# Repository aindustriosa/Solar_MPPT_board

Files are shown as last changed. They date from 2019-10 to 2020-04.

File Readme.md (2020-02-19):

# Propósito
Con este proxecto pretendemos crear unha pequena plataforma educacional de xestión de enerxía solar baseada no Hardware e Software empregado por un dos equipos da Industriosa participante nas edicións 2018 e 2019 da Regata Solar de Marine Instruments coa que obtivemos a victoria en ambas edicións na categoría Open.

https://www.regatasolar.org/

A idea é que o sistema sexa o suficientemente sinxelo de montar e integrar que poida ser usado polos equipos de estudantes.

# Técnica

A complexidade de construir un vehículo solar sen acumulación de enerxía radica en conseguir exprimir ó máximo as posibilidades do panel solar.
Os paneles entregan enerxía eléctrica seguindo unha curva característica que fai necesaria unha xestión intelixente da demanda do sistema de propulsión. É necesario atopar o punto de máxima potencia: se demandamos menos do que o panel é capaz de entregar, desaproveitamos enerxía, e se demandamos máis do que é capaz de entregar, o panel vense abaixo e a potencia entregada cae dramáticamente ata provocar un apagado do sistema.

A continuación unha curva característica de entrega de potencia dun panel solar:

<p align="center">
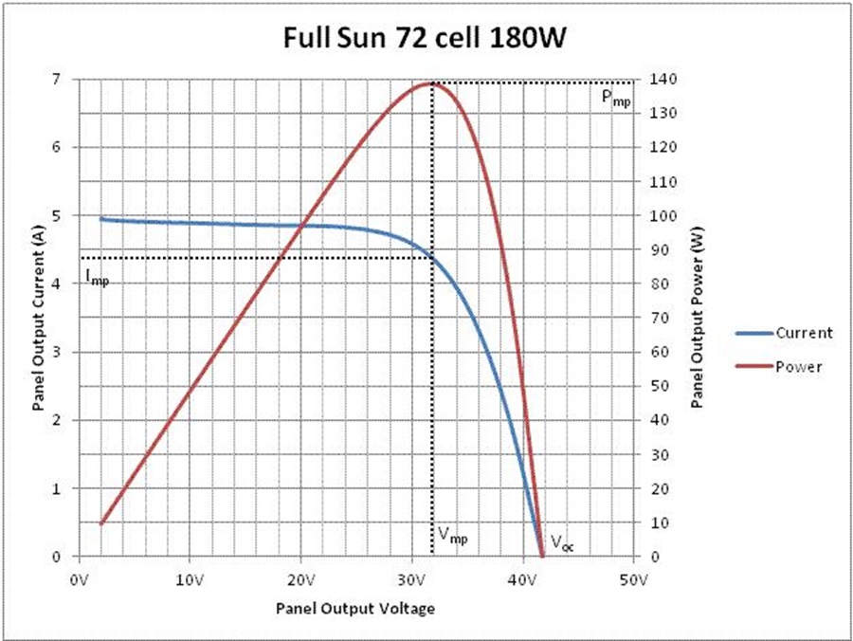
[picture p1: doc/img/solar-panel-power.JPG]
  
</p>

A estratexia seguida para conseguir o propósito consiste en monitorizar constantemente a corrente e tensión entregadas polo panel (e, por tanto, a potencia) e modular mediante un algoritmo software a demanda do motor de propulsión para conseguir en todo momento a máxima potencia disponible.
Este algoritmo ten que ser capaz de auto-adaptarse para facer fronte ás cambiantes condicións nas que o panel se atopa:
* Cambios na radiación solar
* Modificación na posición do panel con respecto do sol
* Cambios na resistencia do motor segundo as condicións dinámicas da embarcación
* ...

# Hardware

A PCB conta con tódolos seus componentes en montaxe Through Hole (Furado pasante) e módulos insertables:
* Arduino Nano
* INA219
* Bluetooth HC-05

<p align="center">
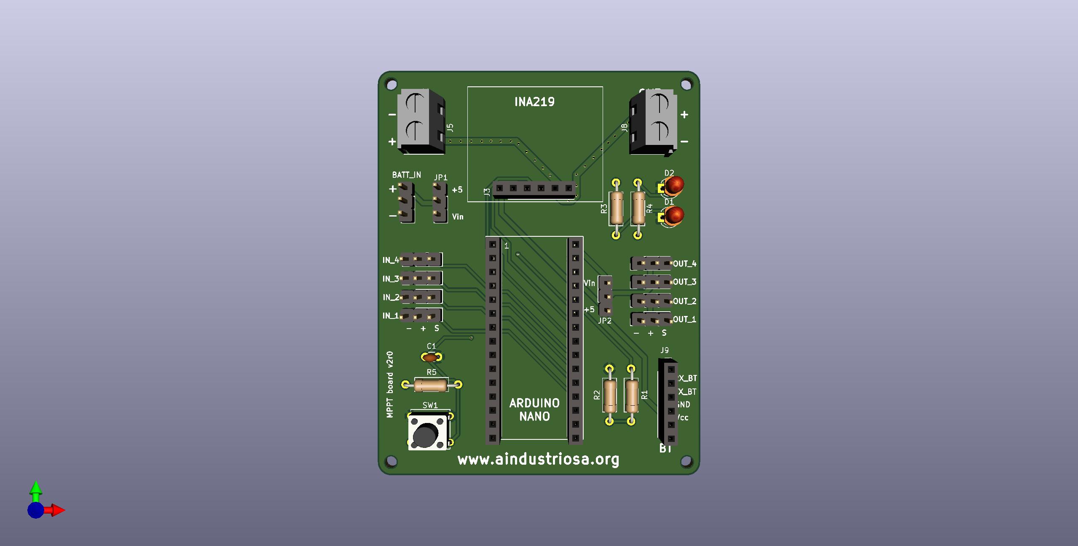
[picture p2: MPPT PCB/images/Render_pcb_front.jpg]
  
</p>

E conexións cos diferentes elementos que compoñen toda a electróncia do barco solar:
* Entrada de panel solar
* Saída de alimentación para o ESC
* Entrada de batería (receptor R/C)
* 4x Entradas PWM de sináis provintes do receptor de R/C
* 4x Saídas PWM para ESC, Servos, ...
* Conexión módulo Bluetooth HC05

Esquema básico de montaxe:

<p align="center">
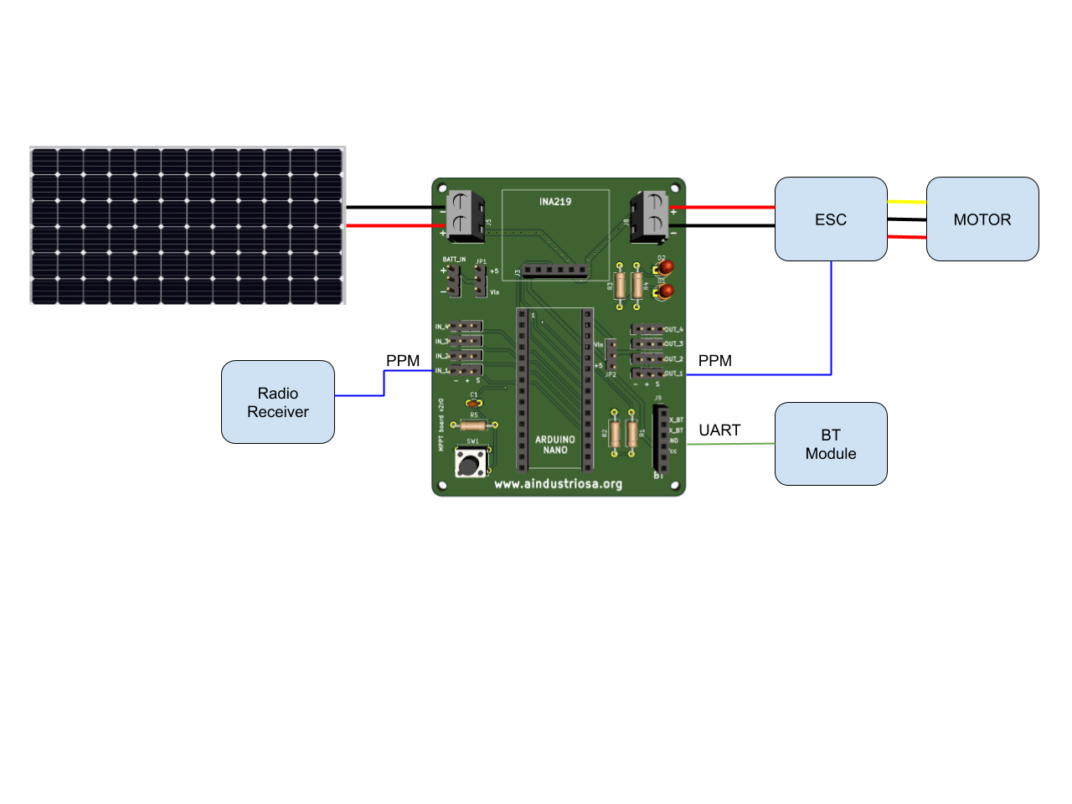
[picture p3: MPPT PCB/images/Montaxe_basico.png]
  
</p>

Os jumpers JP1 e JP2 sirven para conectar os rails de 5V e/ou Vin cos pines de alimentación das entradas e saídas PPM.
Nesta montaxe, se queremos alimentar todo o sistema a través do BEC do ESC conectaremos JP2 con Vin (caso de BEC de 6V) ou con +5V (caso de BEC de 5V). Para alimentar o receptor de radio, conectaremos JP1 para que no pin de alimentación das entradas esté disponible +5V ou Vin, según se desexe.

Na wiki do proxecto detállase o pinout dos diferentes conectores. Recoméndase revisar o esquemático para ter completamente claro o uso de estos jumpers.

https://github.com/aindustriosa/Solar_MPPT_board/wiki

### NOTA: A PCB do INA219 debe ser modificada para poder medir corrente no rango que entrega o panel. Recoméndase sustituir a resisntencia de Shunt orixinal de 0R1 por unha de 0R025.

# Software

A peza principal do código é unha implementación do algoritmo MPPT "Perturb and Observe".
Sirva como guía para comprender a implementación o seguinte documento:

http://ww1.microchip.com/downloads/en/appnotes/00001521a.pdf

En esencia, o algoritmo adapta a demanda que se fai do motor do seguinte modo:
1. Mide Corrente entregada polo panel
2. Mide a Tensión á saída do panel
3. Calcula a potencia
4. Compara coa potencia na anterior iteración
5. Incrementa ou decrementa PWM (ver grafo)

<p align="center">
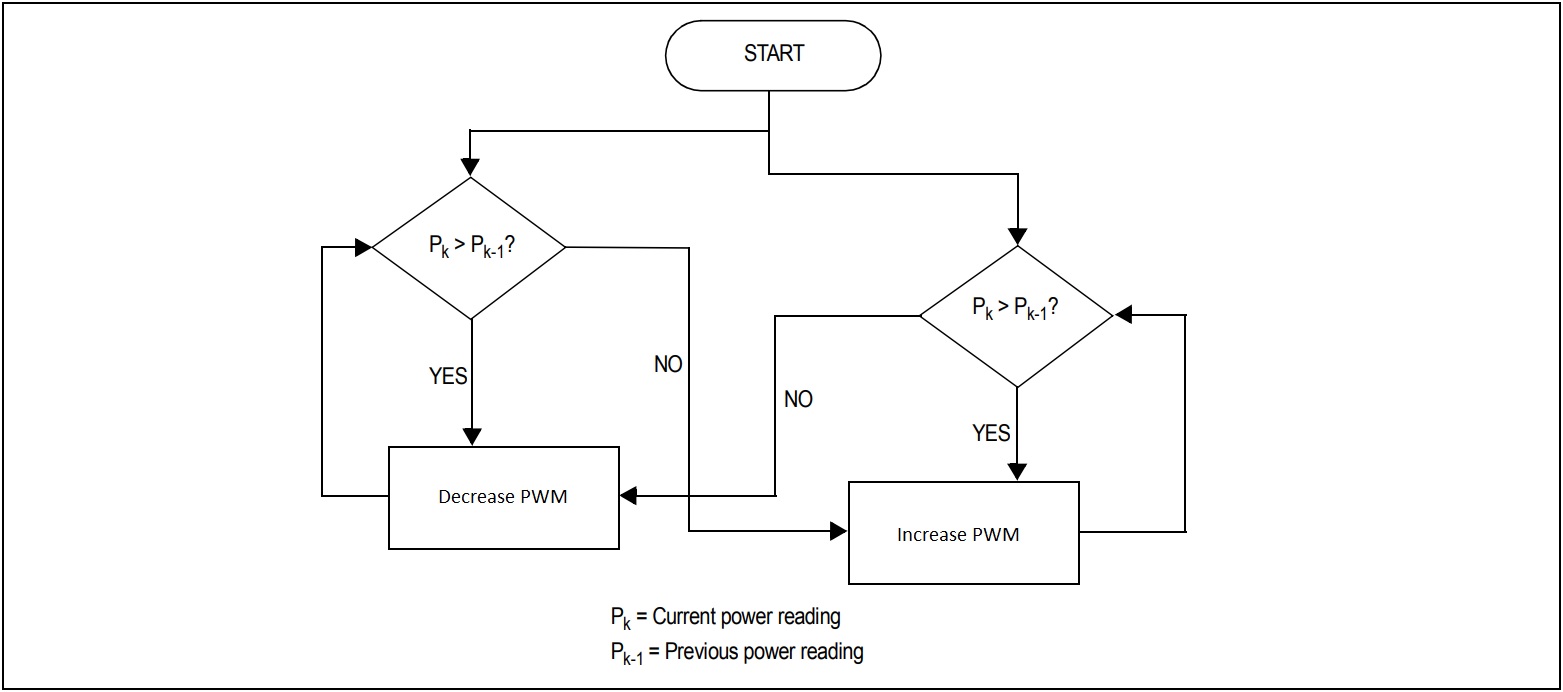
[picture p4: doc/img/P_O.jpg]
  
</p>

# Licenza

## Hardware

Diseñado por Luis Miranda e Hernán Serrano baixo licenza CERN OPEN HARDWARE LICENCE v1.2 http://www.ohwr.org/
Esta licenza aplica ós deseños Hardware e documentación contida na carpeta 'MPPT PCB' de este repositorio.

Designed by Luis Miranda & Hernán Serrano under CERN OPEN HARDWARE LICENCE v1.2 http://www.ohwr.org/
This license applies to hardware designs and documentation which reside in the 'MPPT PCB' folder of this repository.

## Software

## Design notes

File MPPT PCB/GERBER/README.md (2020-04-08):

Estos Gerbers foron enviados a JLCPCB.com

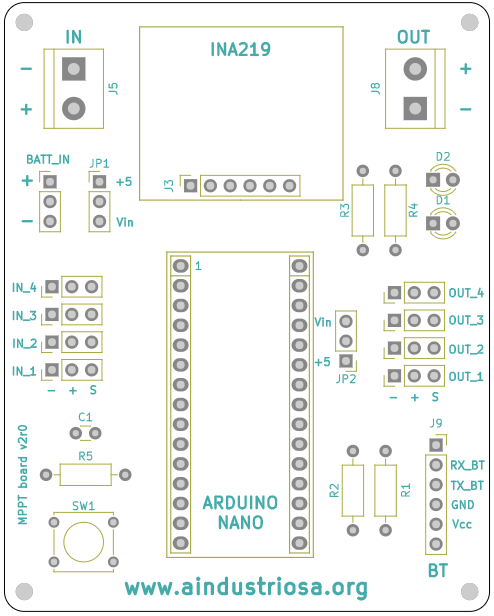
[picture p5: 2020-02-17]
MPPT PCB/images/board_pinout.png

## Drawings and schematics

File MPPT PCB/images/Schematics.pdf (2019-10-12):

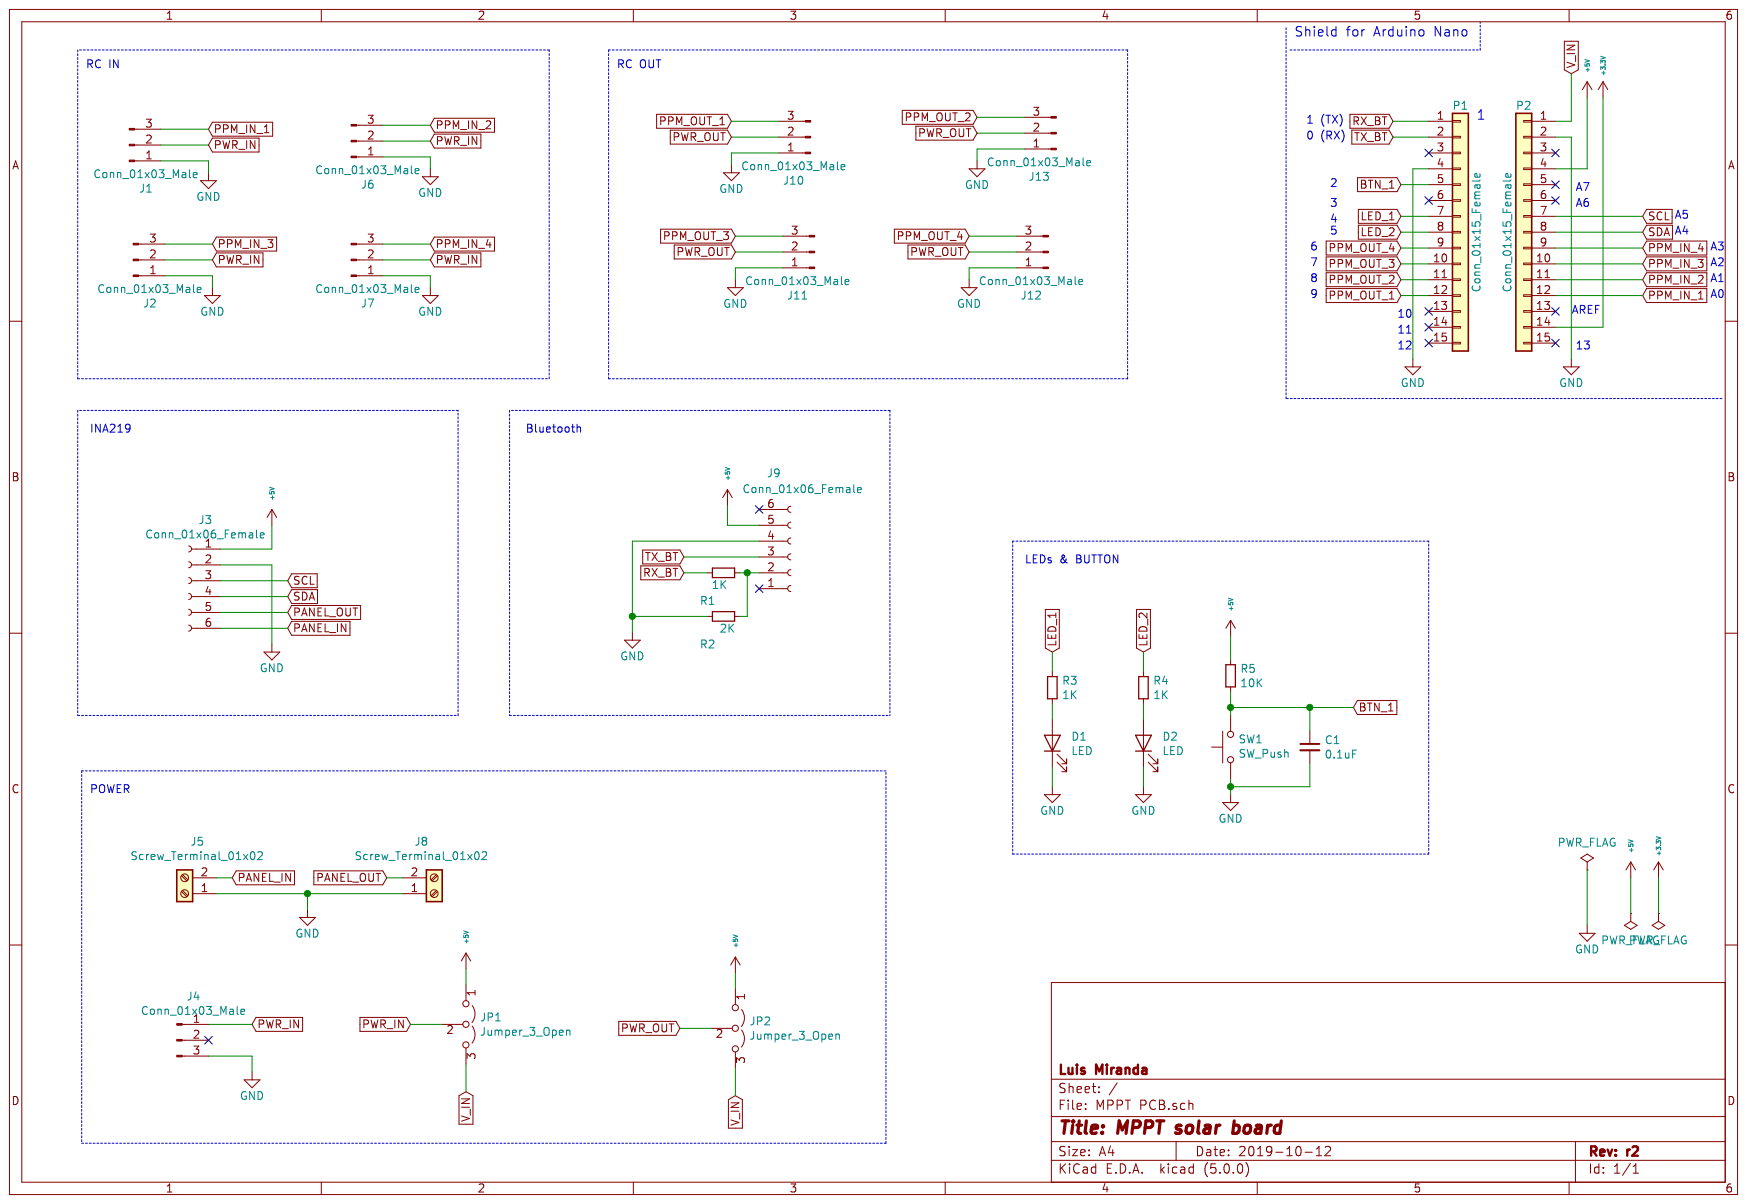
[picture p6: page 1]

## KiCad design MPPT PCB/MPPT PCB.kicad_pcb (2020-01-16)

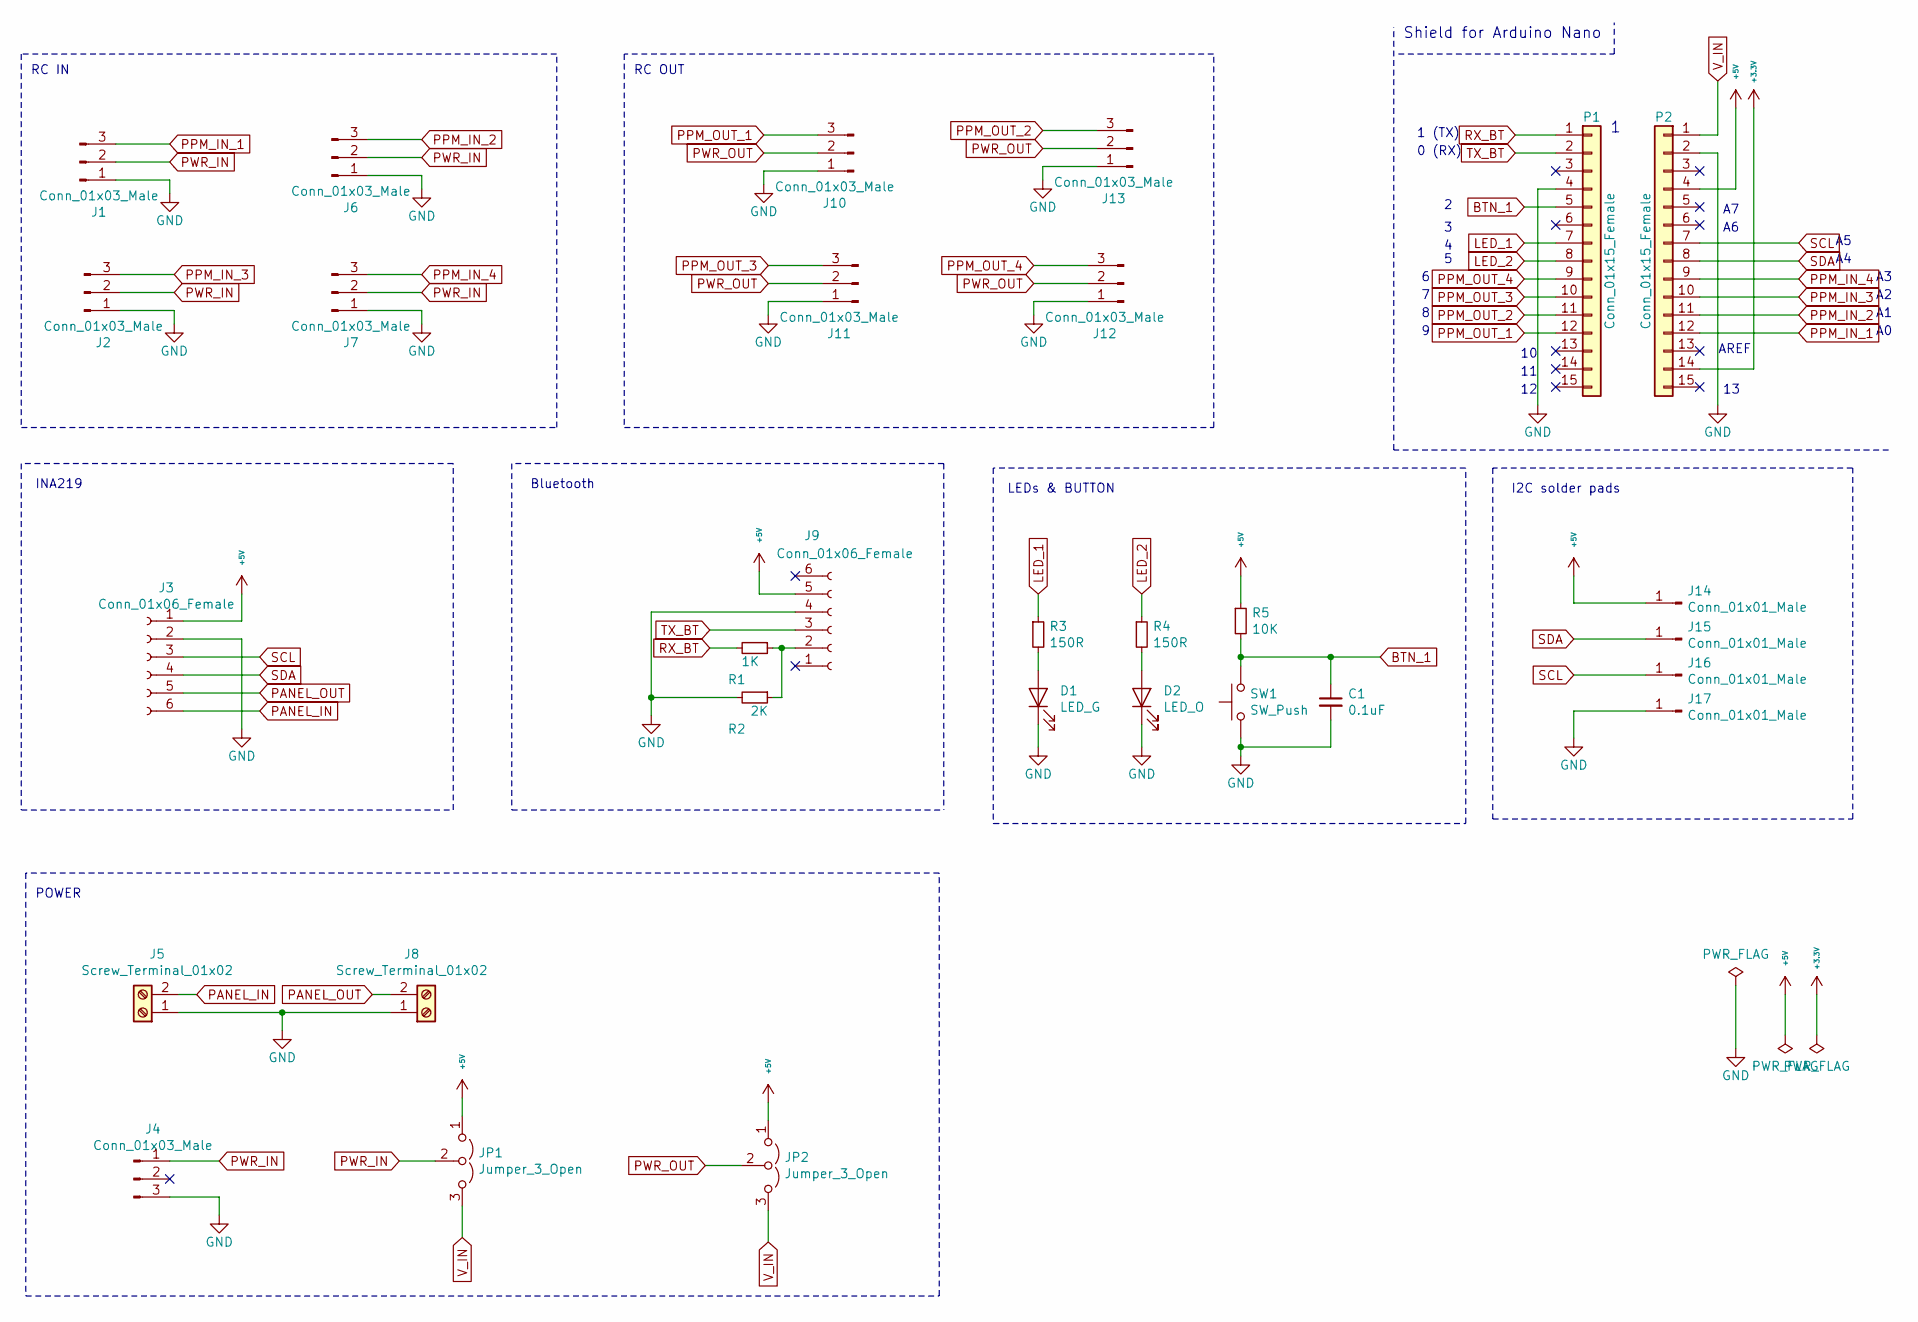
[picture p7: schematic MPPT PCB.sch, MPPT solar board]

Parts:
C1: 0.1uF; C_Disc_D3.0mm_W1.6mm_P2.50mm; DIGIKEY_PN 478-3192-ND
D1: LED_G; LED_D3.0mm; DIGIKEY_PN 732-5008-ND
D2: LED_O; LED_D3.0mm; DIGIKEY_PN 732-5010-ND
J1, J2, J4, J6, J7, J10, J11, J12, J13: Conn_01x03_Male; PinHeader_1x03_P2.54mm_Vertical; DIGIKEY_PN 732-5316-ND
J3, J9: Conn_01x06_Female; PinSocket_1x06_P2.54mm_Vertical; DIGIKEY_PN SAM1213-06-ND
J5, J8: Screw_Terminal_01x02; TerminalBlock_bornier-2_P5.08mm; DIGIKEY_PN A98076-ND
J14, J15, J16, J17: Conn_01x01_Male; Test_Point_2.67x1.02mm
JP1, JP2: Jumper_3_Open; PinHeader_1x03_P2.54mm_Vertical; DIGIKEY_PN 732-5316-ND
P1, P2: Conn_01x15_Female; Socket_Strip_Arduino_1x15; DIGIKEY_PN SAM1213-15-ND
R1: 1K; R_Axial_DIN0207_L6.3mm_D2.5mm_P10.16mm_Horizontal; DIGIKEY_PN CF14JT1K00CT-ND
R2: 2K; R_Axial_DIN0207_L6.3mm_D2.5mm_P10.16mm_Horizontal; DIGIKEY_PN CF14JT2K00CT-ND
R3, R4: 150R; R_Axial_DIN0207_L6.3mm_D2.5mm_P10.16mm_Horizontal; DIGIKEY_PN CF14JT150RCT-ND
R5: 10K; R_Axial_DIN0207_L6.3mm_D2.5mm_P10.16mm_Horizontal; DIGIKEY_PN CF14JT10K0CT-ND
SW1: SW_Push; SW_Tactile_Straight_KSA0Axx1LFTR; DIGIKEY_PN CKN12261-ND

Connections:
+3V3: P2.14
+5V: J3.1, J9.5, J14.1, JP1.1 (A), JP2.1 (A), P2.4, R5.1
BTN_1: C1.1, P1.5, R5.2, SW1.2
GND: C1.2, D1.1 (K), D2.1 (K), J1.1, J2.1, J3.2, J4.3, J5.1, J6.1, J7.1, J8.1, J9.4, J10.1, J11.1, J12.1, J13.1, J17.1, P1.4, P2.2, R2.2, SW1.1
LED_1: P1.7, R3.1
LED_2: P1.8, R4.1
unnamed: D1.2 (A), R3.2
unnamed: D2.2 (A), R4.2
unnamed: J9.2, R1.1, R2.1
PANEL_IN: J3.6, J5.2
PANEL_OUT: J3.5, J8.2
PPM_IN_1: J1.3, P2.12
PPM_IN_2: J6.3, P2.11
PPM_IN_3: J2.3, P2.10
PPM_IN_4: J7.3, P2.9
PPM_OUT_1: J10.3, P1.12
PPM_OUT_2: J13.3, P1.11
PPM_OUT_3: J11.3, P1.10
PPM_OUT_4: J12.3, P1.9
PWR_IN: J1.2, J2.2, J4.1, J6.2, J7.2, JP1.2 (C)
PWR_OUT: J10.2, J11.2, J12.2, J13.2, JP2.2 (C)
RX_BT: P1.1, R1.2
SCL: J3.3, J16.1, P2.7
SDA: J3.4, J15.1, P2.8
TX_BT: J9.3, P1.2
V_IN: JP1.3 (B), JP2.3 (B), P2.1

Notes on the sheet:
Shield for Arduino Nano
1 (TX)
0 (RX)
AREF
RC IN
RC OUT
INA219
Bluetooth
POWER
LEDs & BUTTON
I2C solder pads

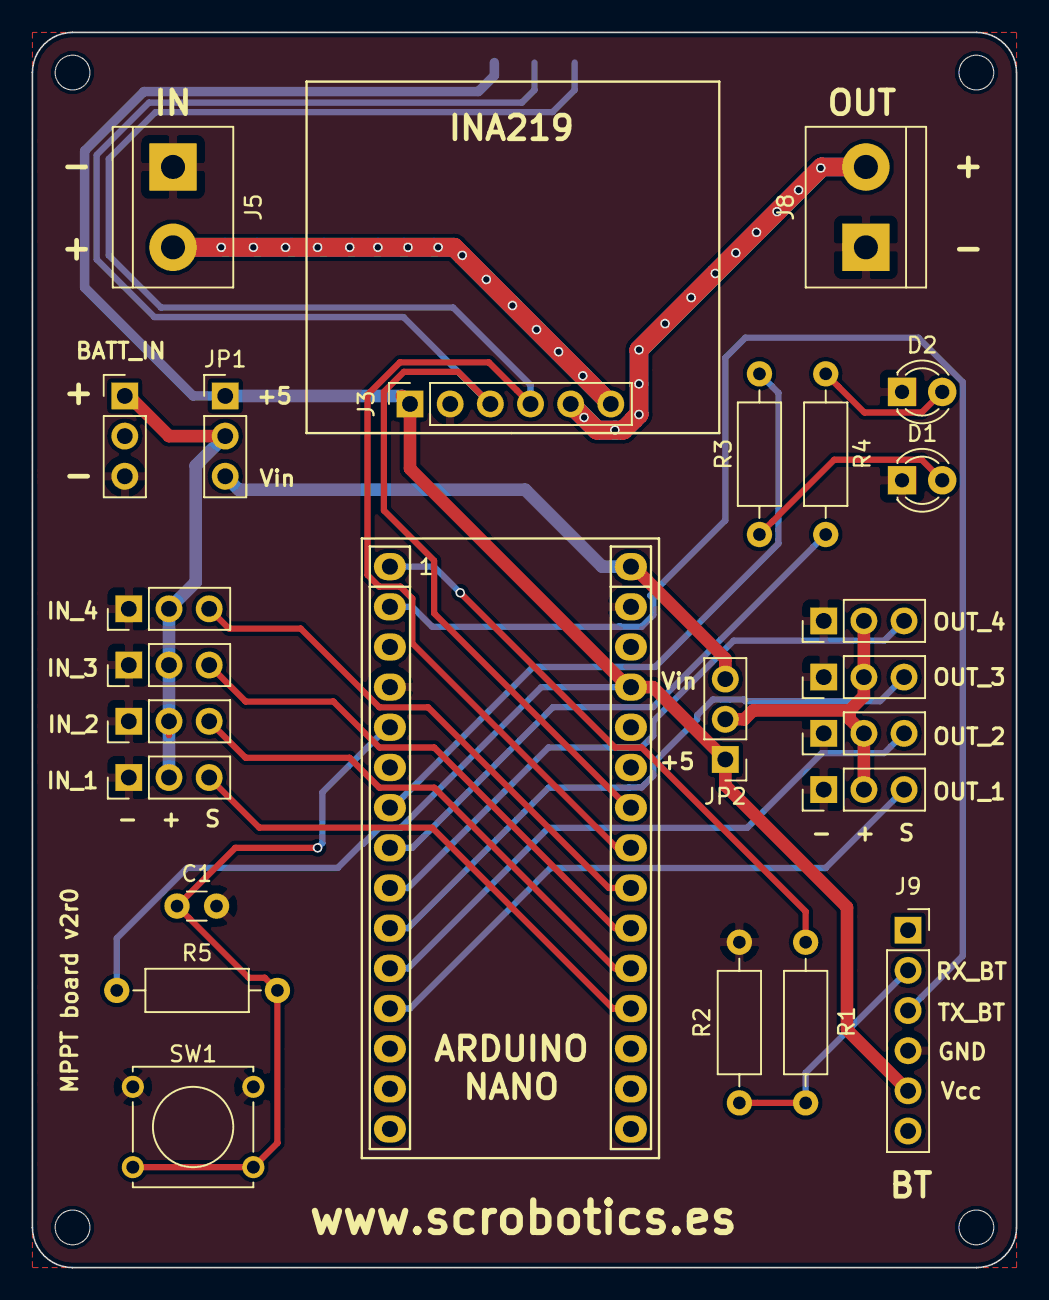
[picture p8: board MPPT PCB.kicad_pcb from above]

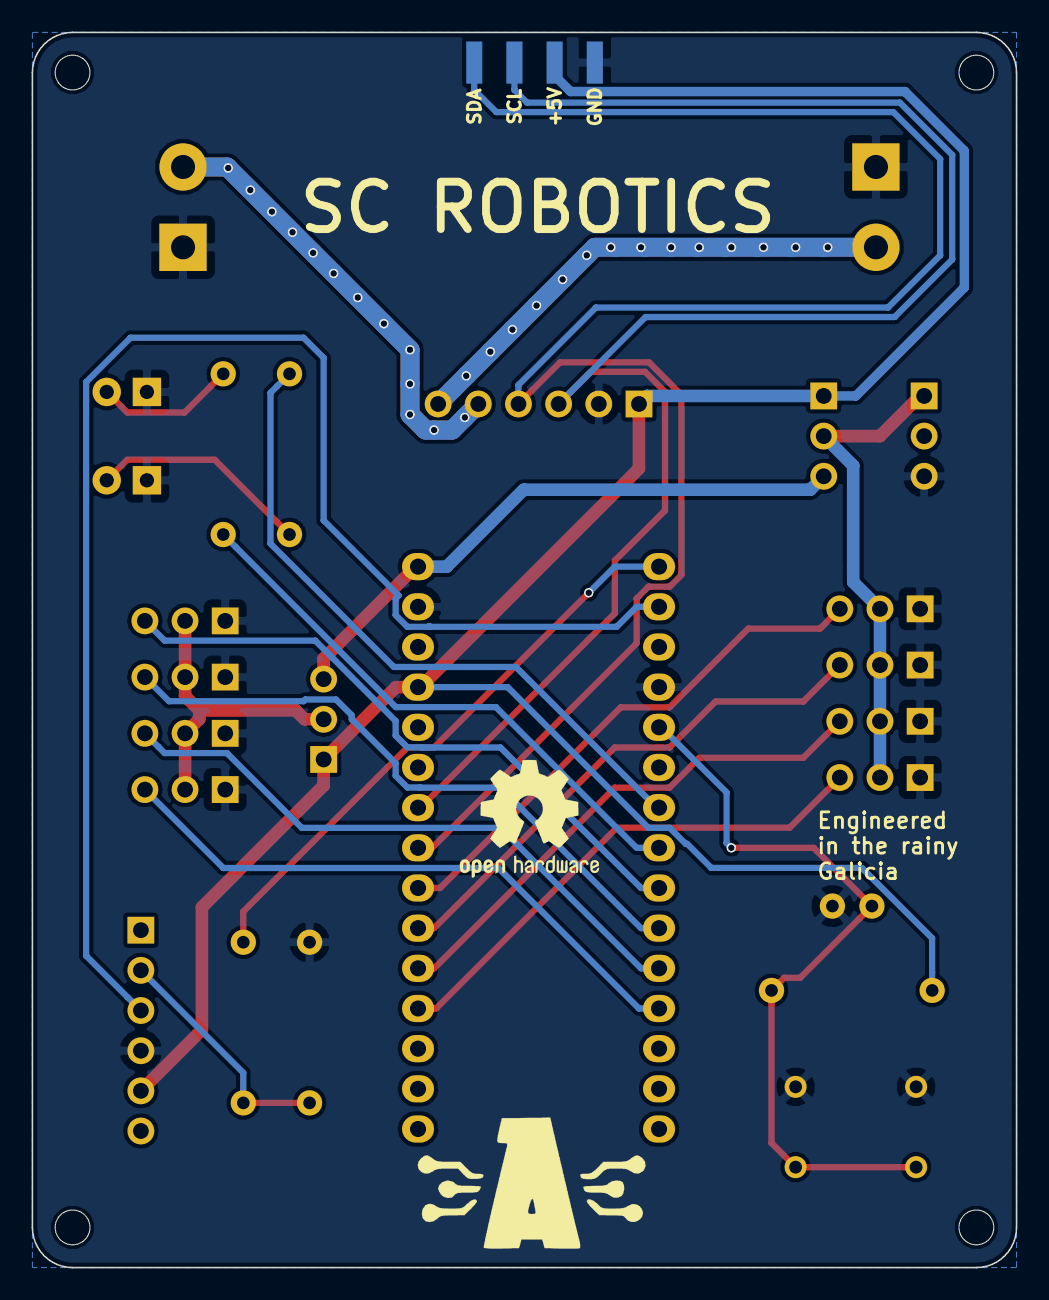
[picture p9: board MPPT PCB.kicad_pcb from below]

Board: 2 copper layers, 62.2 x 78.1 mm, 30 parts (4 on the bottom side), 25 nets.

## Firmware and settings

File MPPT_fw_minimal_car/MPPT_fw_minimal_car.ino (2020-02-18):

#include "esc.h"
#include "Ticker.h"
#include "current.h"
#include "Config.h"

//---------------DEBUG---------------
bool DEBUG = true;

//-------------------P&O Variables--------------
Ticker cicle_timer;
float v = 0;
float i = 0;
float p = 0;
float p_prev = 0;
float v_prev = 0;
int state = 0;

float i_media=0;
float v_media=0;
int cnt_po_ina_samples=0;
void PO_timer_callback();

//-------------------RC SIGNAL-----------------
static byte rcOld;
volatile unsigned long rcRises[4];
volatile unsigned long rcTimes[4];
volatile unsigned int rcChange =0;
void init_RC();

//-----------------ESC----------------------
int PPM1 = 50;    
int speed = 50;   // 50 para configuración bidireccional, 0 para unidireccional

//-----------------INA219---------------
#define Ki 270    // coeficiente de axuste de corrente, pola modificación da resistencia Shunt


ISR (PCINT1_vect){
  byte rcNew = PINC & 15; //PINC & 1111 pilla el estado de los pines A0-A3
  byte changes = rcNew^rcOld; //saca el pin que ha cambiado comparando el estado de los 4 anteriores cn s 4 nuevos
  byte channel =0;
  unsigned long now=micros();
  while(changes){ // de 0000 a 1111
    if((changes &1)){ //Ha cambiado este canal ?
      if((rcNew & (1<<channel))){ //si es flanco subida
        rcRises[channel] =  now;  //t0=ini
      }else{                      //si es flanco bajada
        rcTimes[channel] = now -rcRises[channel];//t1=nw-t0;
      }
    }
    changes >>=1;
    ++channel;
    ++rcChange; //activamos la flag de nuevos cambios para el loop
  }
  rcOld = rcNew;
}


void setup() {
  pinMode(LED1, OUTPUT);
  pinMode(LED2, OUTPUT);
  Serial.begin(9600);
  digitalWrite(LED1,HIGH);
  digitalWrite(LED2,HIGH);
  
  init_ESC();
  delay(1000);
  init_RC();

  digitalWrite(LED1,HIGH);
  digitalWrite(LED2,HIGH);
  
  init_INA219(0);

  cicle_timer.setCallback(PO_timer_callback);
  cicle_timer.setInterval(CICLE_TIMER/CICLE_SAMPLES);                                                                                                                                                                                                                                                                                                                                                                                                                                                                                                                                                                                                                                                                                                                                                                                                                                                                                                                                                                                                                                                                                                                                                
  cicle_timer.start();

  Serial.println("TX_PPM,ESC_PPM,Voltage,Current,Power,State");

  delay(1000);

}


void loop() {
  unsigned long rcT[4];
  unsigned int rcN;

  if(rcChange){
    cli();
    rcN=rcChange;
    rcChange =0; //borramos la flag de nuevos cambios
    //leemos los registros de tiempos d cada puerto
    rcT[0] = rcTimes[0];
    rcT[1] = rcTimes[1];
    rcT[2] = rcTimes[2];
    rcT[3] = rcTimes[3];
    sei();

    PPM1 = map(rcT[0],1000,2000,0,100);

    if(PPM1 >100) PPM1=100;
    if(PPM1 <0) PPM1 = 0;
  }
  sei();
  cicle_timer.update();
}

void print_telemetry(){
    Serial.print(PPM1);
    Serial.print(",");
    Serial.print(speed);
    Serial.print(",");
    Serial.print(v);
    Serial.print(",");
    Serial.print(i);
    Serial.print(",");
    Serial.print(p);
    Serial.print(",");
    switch (state) {
      case AVANCE:
        Serial.println("AVANCE");          
      break;
      case LIMITADO:
        Serial.println("LIMITADO");          
      break;
      case REVERSA:
        Serial.println("REVERSA");          
      break;
    }
    

}

void PO_timer_callback(){ 

        
        if(cnt_po_ina_samples<CICLE_SAMPLES){ //samplea cada 150/10 --> 15ms
            v_media += get_LoadVolts();
            i_media += get_LoadCurrent()/Ki;
            cnt_po_ina_samples++;

        }
        else{ // Al los n samples se ejecuta la máquina de estados

            v = v_media/CICLE_SAMPLES;
            i = i_media/CICLE_SAMPLES;
            p = i*v;

            switch (state) {
              case AVANCE:
                if (PPM1<50) {
                  state=REVERSA;
                  break;
                }
                if (v<UMBRAL_VOLT) state=LIMITADO;
                if (speed < PPM1) speed = speed + PPM_INCREMENTO;
                else speed = PPM1;
                digitalWrite(LED1,HIGH);
                digitalWrite(LED2,LOW);
              break;
              case LIMITADO:
                if (PPM1<50) {
                  state=REVERSA;
                  break;
                }
                if (v>UMBRAL_VOLT) state=AVANCE;
                else speed = speed - PPM_DECREMENTO;
                if (speed<50) speed=50;
                digitalWrite(LED1,LOW);
                digitalWrite(LED2,HIGH);
              break;
              case REVERSA:
                if (PPM1<45) speed=REV_SPEED; //hacia atrás, velocidad fija
                if (PPM1>=50) state=AVANCE;
                digitalWrite(LED1,LOW);
                digitalWrite(LED2,LOW);
              break;
              default:
              // statements
              break;
            }
            
            
         
         vel_ESC(speed); 
         p_prev=p;    
         v_prev=v;

         v_media = 0;
         i_media = 0;
         cnt_po_ina_samples = 0; //reseteamos contador de samples para k comience con los sig 10

         if(DEBUG){
            print_telemetry();
         }
      }//end if vel o P&or



} //end callback

void init_RC(){
  rcOld =0;
  pinMode(A0,INPUT);
  pinMode(A1,INPUT);
  pinMode(A2,INPUT);
  pinMode(A3,INPUT);
  PCMSK1 |= 0x0F; //pin-change interrupt en los 4 primeros pines del PORTC (A0-A3)
  PCIFR |= 0x02; //clear pin-change interrupt
  PCICR |= 0x02; //pin-change interrupt enable
}

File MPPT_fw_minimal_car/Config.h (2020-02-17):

// Definición de pines de Arduino Nano
#define LED1 4
#define LED2 5
#define BTN 2
#define PPM_OUT_1 9
#define PPM_OUT_2 8
#define PPM_OUT_3 7
#define PPM_OUT_4 6
#define PPM_IN_1 A0
#define PPM_IN_2 A1
#define PPM_IN_3 A2
#define PPM_IN_4 A3

// Parámetros de configuración xerais
#define CICLE_TIMER 100   //tempo de ciclo en ms
#define CICLE_SAMPLES 10  //mostras por ciclo
#define PPM_DECREMENTO 3   //cantidade decrementada en caso de limitar
#define PPM_INCREMENTO 2  //aceleración
#define UMBRAL_VOLT 12    //voltaxe por debaixo da cal se limita
#define REV_SPEED 40    //velocidad fija en reversa

// Estados FSM
#define AVANCE 0
#define LIMITADO 1
#define REVERSA 2

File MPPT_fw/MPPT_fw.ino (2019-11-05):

#include <Streaming.h> //para la salida de print y endl http://arduiniana.org/libraries/streaming/
#include <EEPROM.h>
#include "esc.h"
#include "Ticker.h"
#include "current.h"
#include "Config.h"

#define LED1 4
#define LED2 5
#define BTN 2

//---------------DEBUG---------------
//#define PIN_DEBUG 8
bool DEBUG = true;
//-------------------P&O SETTINGS--------------
Ticker PO_timer;

#define PO_ENABLE_SPEED 30
#define PO_TIMER 150
#define PO_STEP 1
#define po_samples 10
float v = 0;
float i = 0;
float p = 0;
float Av = 0; //Delta Volts
float Ap = 0; //Delta Power
float p_prev = 0;
float v_prev = 0;

float i_media=0;
float v_media=0;
int cnt_po=1;
int cnt_po_ina_samples=0;
int po_speed =0; //valor d po_speed cuando entramos en po
bool po_enable= false;
void PO_timer_callback();

//-------------------RC SIGNAL-----------------
static byte rcOld;
volatile unsigned long rcRises[4];
volatile unsigned long rcTimes[4];
volatile unsigned int rcChange =0;
void init_RC();

//-----------------ESC----------------------
#define sensibilidad 3
int speed = 0;

//-----------------INA219---------------
#define Ki 270
#define Kv 

//--------------THERMISTOR--------------
#define th1 A6
#define th2 A7

int temp1,temp2 =0;


ISR (PCINT1_vect){
  byte rcNew = PINC & 15; //PINC & 1111 pilla el estado de los pines A0-A3
  byte changes = rcNew^rcOld; //saca el pin que ha cambiado comparando el estado de los 4 anteriores cn s 4 nuevos
  byte channel =0;
  unsigned long now=micros();
  while(changes){ // de 0000 a 1111
    if((changes &1)){ //Ha cambiado este canal ?
      if((rcNew & (1<<channel))){ //si es flanco subida
        rcRises[channel] =  now;  //t0=ini
      }else{                      //si es flanco bajada
        rcTimes[channel] = now -rcRises[channel];//t1=nw-t0;
      }
    }
    changes >>=1;
    ++channel;
    ++rcChange; //activamos la flag de nuevos cambios para el loop
  }
  rcOld = rcNew;
}


void setup() {
  Serial.begin(9600);

  //pinMode(PIN_DEBUG,INPUT);

  init_ESC();
    delay(1000);
  init_RC();
  
  init_INA219(0);

  PO_timer.setCallback(PO_timer_callback);
  PO_timer.setInterval(PO_TIMER/po_samples);                                                                                                                                                                                                                                                                                                                                                                                                                                                                                                                                                                                                                                                                                                                                                                                                                                                                                                                                                                                                                                                                                                                                                
  PO_timer.start();

  po_enable = false; //indicamos que iniciamos en speed
  Serial.println("TX_PPM,Mode,ESC_PPM,Voltage,Current,Power");
  Serial.println();

}


void loop() {
  unsigned long rcT[4];
  unsigned int rcN;

  if(rcChange){
    cli();
    rcN=rcChange;
    rcChange =0; //borramos la flag de nuevos cambios
    //leemos los registros de tiempos d cada puerto
    rcT[0] = rcTimes[0];
    rcT[1] = rcTimes[1];
    rcT[2] = rcTimes[2];
    rcT[3] = rcTimes[3];
    sei();

    speed = map(rcT[0],1000,2000,0,100);
    //speed = speed/sensibilidad;

    if(speed >100){
        speed=100;
    }
    //Serial.println(rcT[0]);
  }
  sei();
  PO_timer.update();
}

void print_telemetry(){
    Serial.print(speed);
    Serial.print(",");
    if(po_enable){
        Serial.print("10,"); //modo P
        Serial.print(po_speed);
        digitalWrite(LED1,HIGH);
        digitalWrite(LED2,LOW);
    }else{
        Serial.print("5,"); // modo s
        Serial.print(speed);
        digitalWrite(LED1,LOW);
        digitalWrite(LED2,HIGH);
    }
    Serial.print(",");
    Serial.print(v);
    Serial.print(",");
    Serial.print(i);
    Serial.print(",");
    Serial.println(p);
    //Serial.print(Ap);
    //Serial.print(Av);
    //Serial.println(analogRead(th1));
}

void PO_timer_callback(){ 

        if(cnt_po_ina_samples<po_samples){ //samplea cada 150/10 --> 15ms
            v_media += get_LoadVolts();
            i_media += get_LoadCurrent()/Ki;
            cnt_po_ina_samples++;

        }else{ // Al los 10 samples 10*15 --> 150ms se ejecuta el P&O

            v = v_media/po_samples;
            i = i_media/po_samples;
            p = i*v;
            Av = v - v_prev;
            Ap = p - p_prev;

            //DEBUG = digitalRead(PIN_DEBUG);
            if (speed<0) speed=0;
            if(speed < PO_ENABLE_SPEED){ //Si po_speed <50, vel fijada x mando
                po_enable=false; //indicamos que estamos en modo speed
                vel_ESC(speed);
                cnt_po =1; //reseteamos indicador de P&O para que cuando comience se resetee en ciclo 1 y pille speed       
            }else{ //Si po_speed >50 entra P&0
                /*
                ----------COMIENZA P&O--------------------
                */
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

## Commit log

2019-10-08 PCB proto version
    [MPPT PCB.kicad_pcb, MPPT PCB.sch]
2019-10-12 Minor changes. Added images.
    [MPPT PCB.sch]
2019-10-12 Fixed servo pinout (Input and Output)
    [MPPT PCB.kicad_pcb, MPPT PCB.sch]
2020-01-16 Version 2 of PCB
    [MPPT PCB.kicad_pcb, MPPT PCB.sch]
2020-01-16 Changed front PCB render
2020-01-20 Added PCB BOM
2020-02-17 Add minimal car firmware for MPPT board
2020-02-18 Fix LED output pin configuration and colour
    [MPPT_fw_minimal_car.ino]
2020-04-08 Add gerber files
    [MPPT PCB-B_Cu.gbr, MPPT PCB-B_Mask.gbr, MPPT PCB-B_Paste.gbr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]
